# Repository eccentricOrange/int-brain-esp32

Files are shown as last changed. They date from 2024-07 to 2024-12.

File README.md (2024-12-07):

# Integrated Brain
The Integrated Brain is a custom PCB designed to control, supply power to, and monitor a four-wheeled robot. It's built on a master-slave architecture, with an ESP32 as the slave and an SBC (such as an NVIDIA Jetson or Raspberry Pi) as the master.

## Features
| Feature | Description | Specification |
| --- | --- | --- |
| ESP32 Microcontroller | Header for external ESP32 | **ESP32-WROOM-32** 38-pin dev board |
| Motor Drivers | Built on to the PCB | 4x **DRV8251A**. While the 8251A can provide up to **4.1 A**, the PCB design is compatible with other DRV series drivers too. |
| Motor Indicator LEDs | Built on to the PCB | 4x, user-controllable through the PWM demux. |
| Motor Encoder | Support for external quadrature encoders | Connect through JST-4 connectors, directly to ESP32 GPIO. |
| Motor Current Sense | Built on to the PCB | Using the 8251A's feature, connected to the ESP32 ADCs. Additional support for shunt resistor and current-sense amplifier in case of different motor driver IC. |
| IMU | Headers for external IMU | **MPU9250** connected over I2C0 to the ESP32 |
| Internal power supply | Built on to the PCB | **5V (5A)** (TPS5450 buck) and **3.3V** (AMS1117) power supplies for the ESP32 and other peripherals. |
| SBC Power supply | Built on to the PCB | **5V (5A)** (TPS5450 buck) power supply for the SBC., via USB-A. |
| PWM Demux | Built on to the PCB | **PCA9635** connected over I2C0 to the ESP32. Spare PWM channels are *not* exposed. |

## Overall system architecture
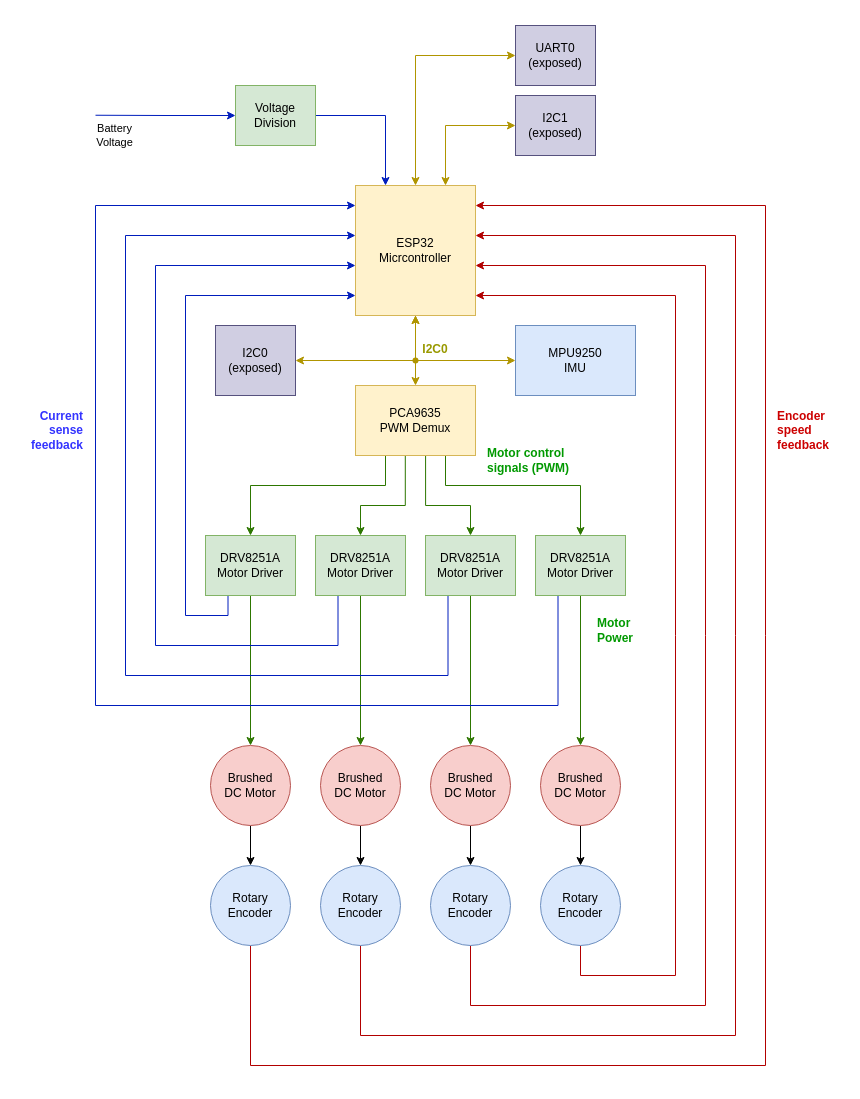
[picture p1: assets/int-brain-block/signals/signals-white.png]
block


The ESP32 microcontroller handles the interaction between all the different peripherals, along with low-level control loops and signal processing. Telemetry and IMU data is fed directly to this ESP32.

Motors are driven using full H-bridge drivers, with built-in braking and current-sense capabilities. These motor drivers are controlled through a PWM demux, owing to the requirement for a large number of PWM pins.

Signals on-board are handled over I2C0, where the ESP32 acts as the master. It is configured as a slave on the I2C1 bus, which is used to communicate with an SBC. I2C0, I2C1, as well as an additional UART port are all exposed with JST connectors.

## Responsibilities of the ESP32 microcontroller
*   Receive commands from the SBC over I2C1
*   Control the motor drivers and the motor indicator LEDs, using the PCA9635 PWM mux over I2C0
*   Read the motor encoders and the motor current sense
*   Read the IMU data, over I2C0
*   Read the battery voltage (using a voltage divider)
*   Run the internal PID loop for motor control (RPM using encoder data)
*   Handle motor protection in case of stall (detected by encoder data) or disconnect (detected by current sense)
*   Filter IMU data
*   Send data to the SBC over I2C1 when requested

## Motor driver design
The system is designed to use the Texas Instruments DRV8251A motor driver, which is capable of driving up to 4.1 A.

Provided that DRV8251A (or any other DRV82\*\*A) drivers are used, we can leverage both the current-sense and current-limiting capabilities of the chip. Since the driver handles current attenuation, we may use a low-power high-resistance shunt resistor to generate a voltage drop. Additionally, using this as a voltage divider, we may supply a current limit; beyond this limit, the driver will automatically throttle voltage.

However, if an alternate motor driver is used (such as DRV8251), the system is designed to support a high-power low-resistance shunt resistor and a current-sense amplifier. The current-limiting feature of the driver will not be used in this case.

The equations to calculate these resistances were derived from the DRV8251A data sheet, and are provided in the schematics.

## Power supply design
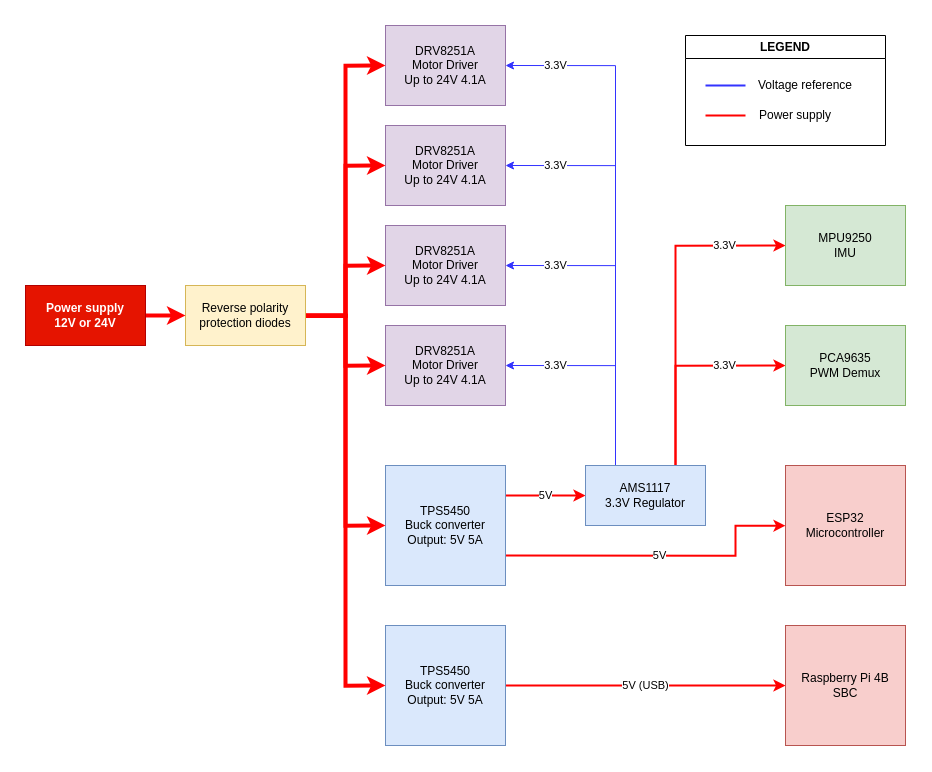
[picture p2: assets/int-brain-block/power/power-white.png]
power


The system is designed to take either 12 V or 24 V DC power. This can be given by either a DC barrel jack or an XT60 connector, designed with the intention of using a LiPo battery. This power must go through two diodes (hooked up in parallel) before being used for any purpose.

Conversion to 5 V and 3.3 V is handled on-board. The buck converter responsible for supplying power to the SBC is isolated from the rest of the system for increased stability.

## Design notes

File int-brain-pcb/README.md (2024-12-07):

# Pin-outs

## IMU MPU9250
| MPU9250 | ESP32 GPIO |
| --- | --- |
| INT | 33 |
| FSYNC | 32 |

Use I2C0 for communication with the IMU.

## Motor Drivers
| Motor | DRV8251A | PCA9685 |
| --- | --- | --- |
| 1A | IN 1 | 12 |
| 1A | IN 2 | 13 |
| 1B | IN 1 | 8 |
| 1B | IN 2 | 9 |
| 2A | IN 1 | 3 |
| 2A | IN 2 | 4 |
| 2B | IN 1 | 5 |
| 2B | IN 2 | 6 |

Use I2C0 for communication with the PCA9685.

## Motor indicator LEDs
| Motor | PCA9685 |
| --- | --- |
| 1A | 11 |
| 1B | 10 |
| 2A | 2 |
| 2B | 7 |

Use I2C0 for communication with the PCA9685.

## Encoders
| Encoder | Pin | ESP32 GPIO |
| --- | --- | --- |
| 1A | 1 | 18 |
| 1A | 2 | 19 |
| 1B | 1 | 23 |
| 1B | 2 | 25 |
| 2A | 1 | 5 |
| 2A | 2 | 17 |
| 2B | 1 | 14 |
| 2B | 2 | 12 |

## Motor current sense
| Motor | ESP32 GPIO |
| --- | --- |
| 1A | 35 |
| 1B | 34 |
| 2A | 39 |
| 2B | 36 |

## Protocols
| Protocol | Pin | ESP32 GPIO | Built-in Pull-up |
| --- | --- | --- | --- |
| I2C0 | SDA | 21 | Yes, 4.7k to 3.3V |
| I2C0 | SCL | 22 | Yes, 4.7k to 3.3V |
| I2C1 | SDA | 13 | Yes, 4.7k to 3.3V |
| I2C1 | SCL | 15 | Yes, 4.7k to 3.3V |
| UART0 | TX | 1 | No |
| UART0 | RX | 3 | No |

Use I2C0 (as master) for communication with the IMU and PCA9685. Use I2C1 (as slave) for communication with an SBC such as a Raspberry Pi or NVIDIA Jetson.

## Miscellaneous
| Function | ESP32 GPIO |
| --- | --- |
| Battery Voltage | 25 |
| Motor PCA Enable | 4 |

# Screenshots

PCB Front
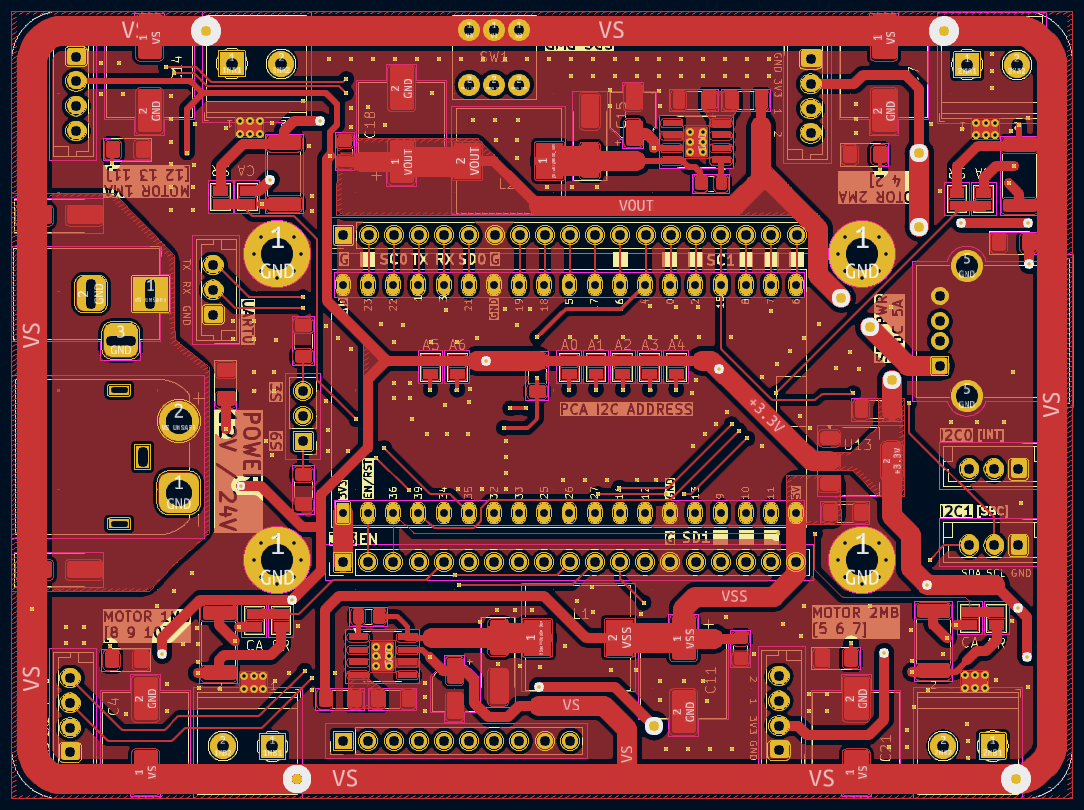
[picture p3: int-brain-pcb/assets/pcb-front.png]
pcb-front


PCB Back
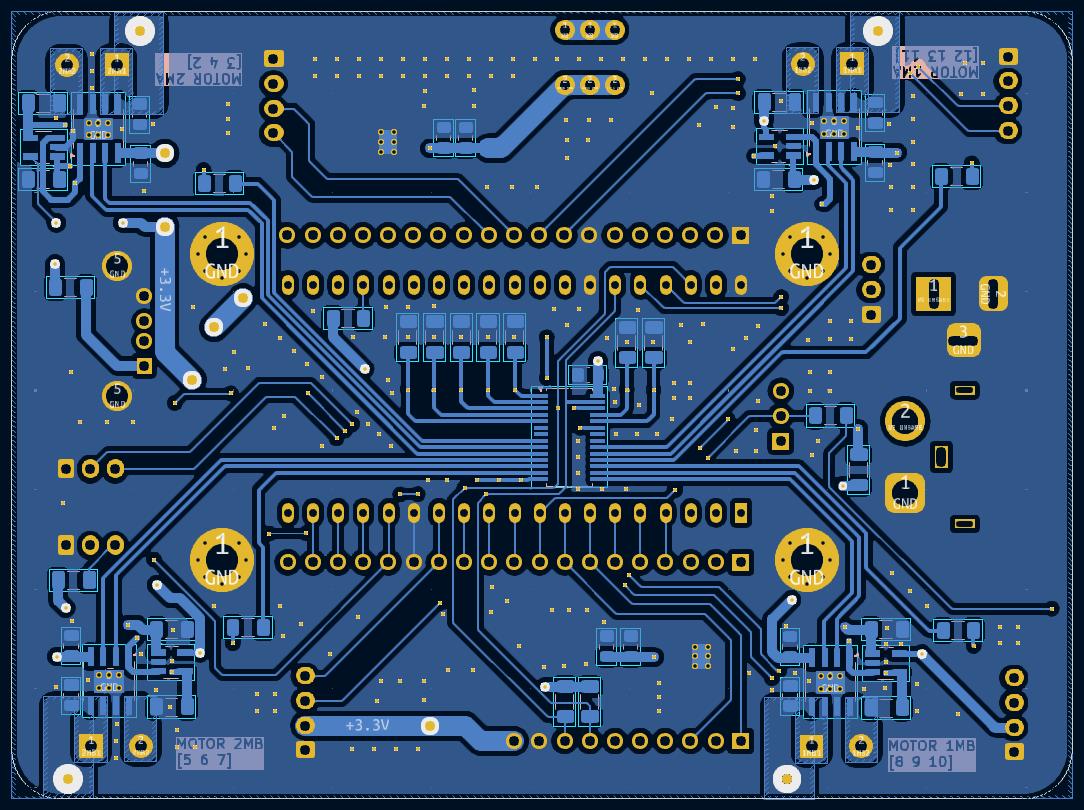
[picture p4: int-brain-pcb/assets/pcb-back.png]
pcb-back


3D Front
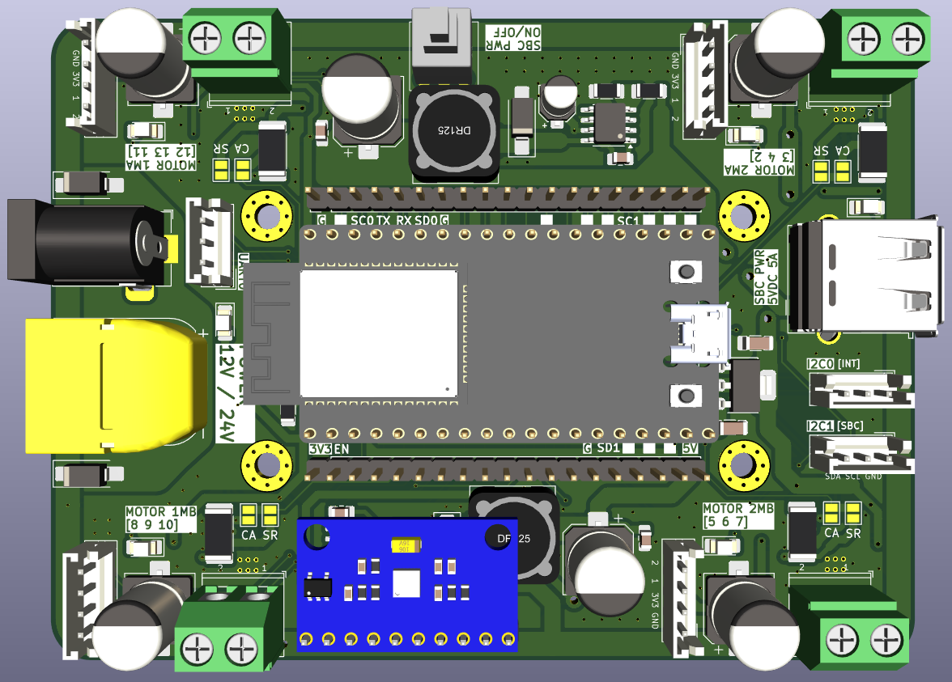
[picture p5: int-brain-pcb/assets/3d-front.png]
3d-front


3D Back
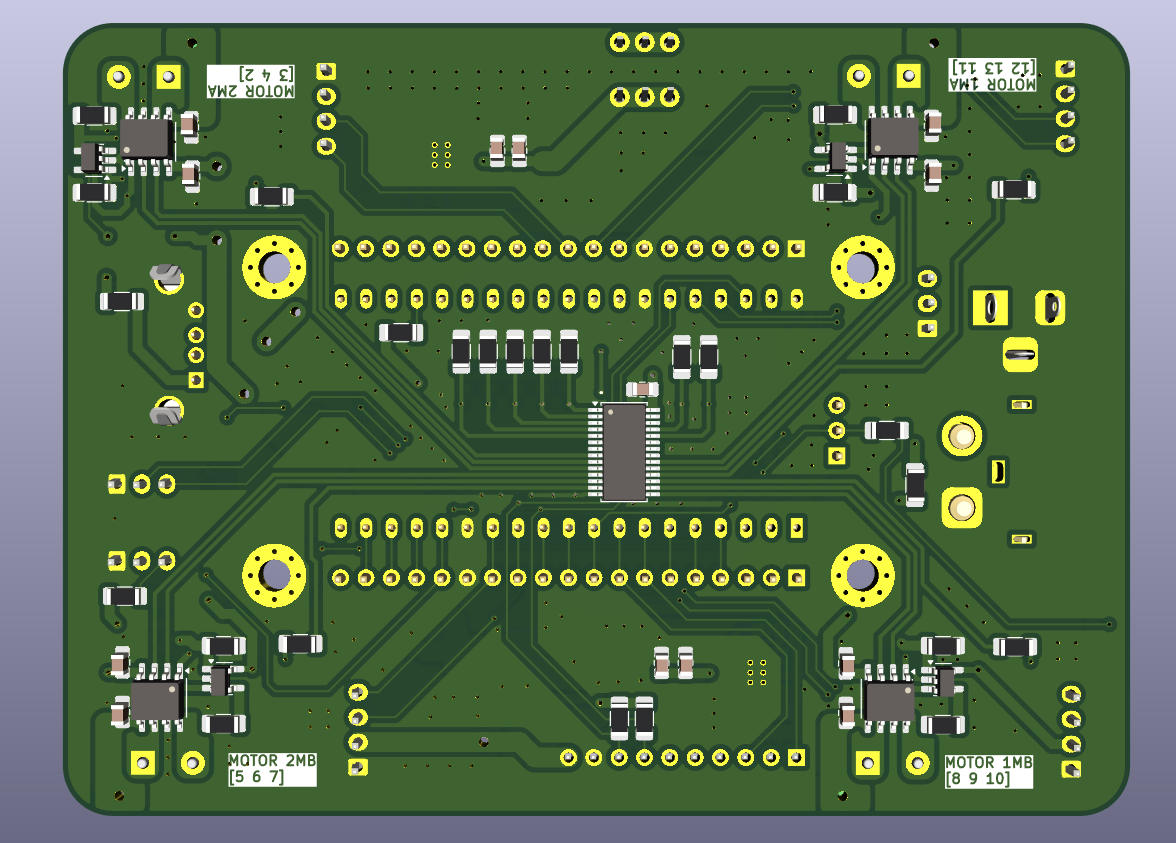
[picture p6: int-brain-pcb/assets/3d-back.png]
3d-back


3D Angled
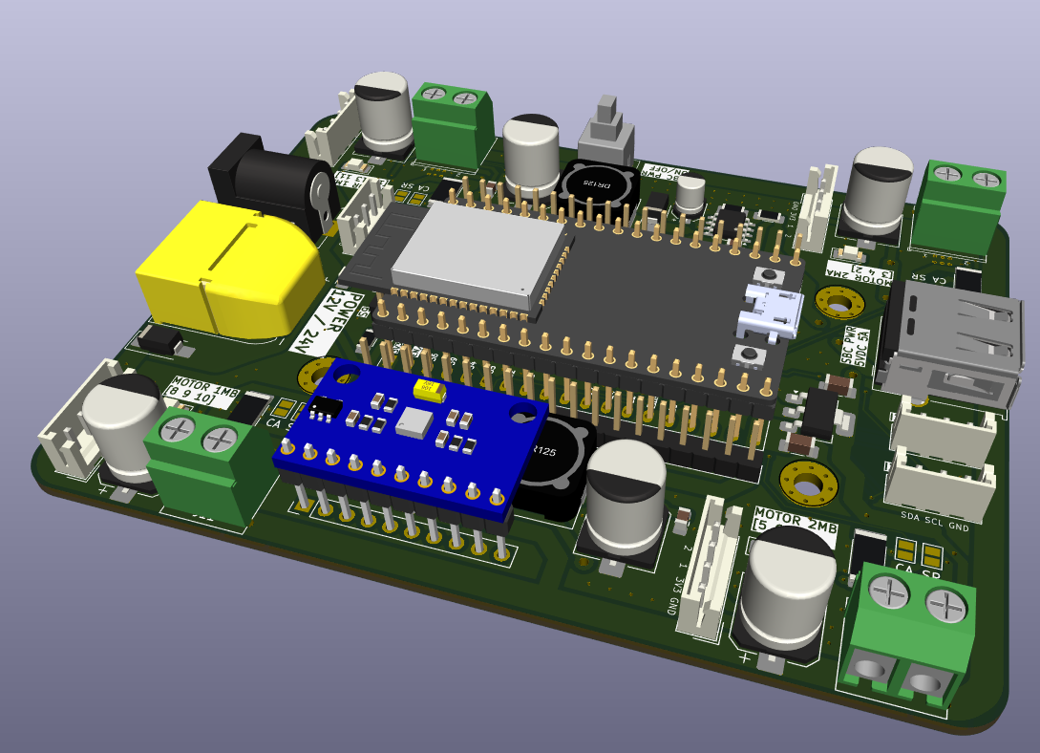
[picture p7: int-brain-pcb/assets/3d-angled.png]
3d-angled


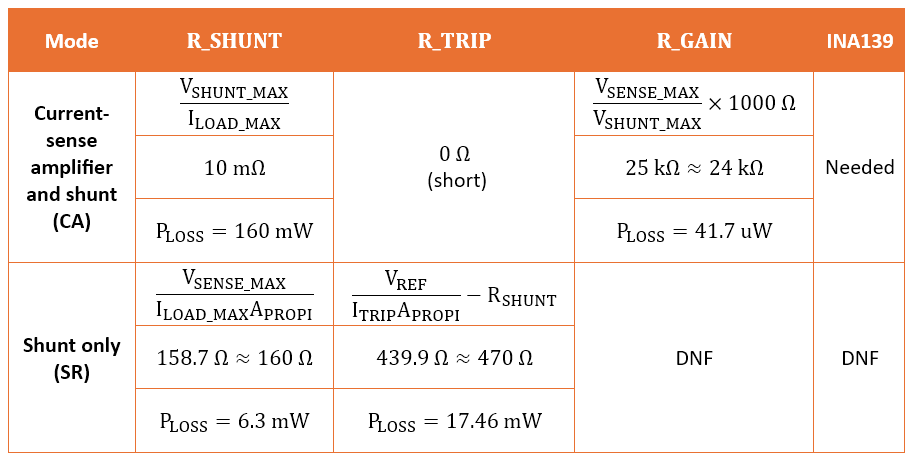
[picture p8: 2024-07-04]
int-brain-pcb/assets/calculated-values.png

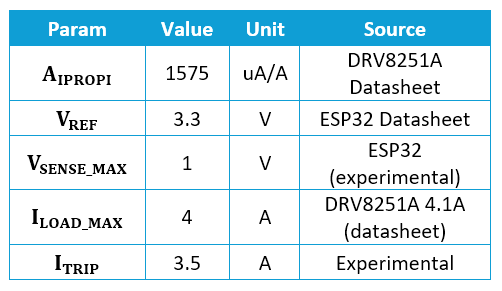
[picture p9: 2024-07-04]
int-brain-pcb/assets/assumed-values.png

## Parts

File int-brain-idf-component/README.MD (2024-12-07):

# Integrated Brain ESP-IDF Component
This is the MCU firmware for a custom PCB designed to control, supply power to, and monitor a four-wheeled robot. It's built on a master-slave architecture, with an ESP32 as the slave and an SBC (such as an NVIDIA Jetson or Raspberry Pi) as the master.

Note that this project has a lot of different registers, addresses, and buffers. These are referenced several times throughout the documentation, but in the interest of comprehensibility, they are all listed towards the end of the documentation only.

# Overall design
Let's get an overview of the different concepts and categories of stuff (such as functions) involved in this component.

## Direct and register-based tasks
In general, there are two types of functions in the component:

-   **Direct task**

    These functions are typical functions. You call them (and pass in arguments if relevant) and the function will try to do whatever you told it to. Exactly how it behaves is completely transparent in this scenario: for example, if you told motor 3 to move forward with a PWM of 127, that's exactly what the system will attempt to do, and nothing else.

-   **Register-based task**

    In the interest of having a flexible system that can establish duplex (two-way) communication with an SBC, there is an extensive system of registers and state variables. Many functions write to these, and many others read from them to decide what actions to perform. You (the programmer) doesn't have the luxury of specifying the 127 (PWM) or forward (direction) as literal values in this situation.

The Doxygen documentation for each function states its type, so you can easily tell which is which.

## Topics/themes

*   **PCA9635 PWM Demux**

    To overcome the low number of GPIOs in the ESP32, this project uses the PCA driver to give PWM signals to the motor drivers and their corresponding LEDs. There are methods around initializing the driver, setting it's mode, setting specific PWM values etc. These are all under `pca_driver.h`.

*   **Current sense**

    The motor drivers have a current sense output that can be read by the ESP32 (with the use of a shunt resistor). The current sense is read by the ADC and converted to a digital value. The initialization, calibration, and reading of the current sense are all under `current_sense.h`.

*   **Encoder**
    
    The motors have encoders that can be read by the ESP32 to provide their angular velocity. The initialization, reading, and resetting of the encoders are all under `encoder.h`.

*   **Control of the robot and that of the motors is separate**

    The PCA drivers file `pca_driver.h` is responsible for controlling the motors and LEDs, and tends to deal with the lower-level functions of one motor at a time. The `four-wheel-robot.h` file is responsible for controlling four motors at a time, and includes some functions to instead treat the system as a cohesive robot. Functions in `four-wheel-robot.h` use functions from `pca_driver.h` quite heavily.

*   **Structure**

    In general, "direct" functions are used to handle things like initialization and register-based functions are used to handle the actual tasks. Either these functions directly, or your custom functions, are expected to be registered as RTOS tasks using `xTaskCreate()` (built-in to FreeRTOS and ESP-IDF) since they will run perpetually.

# I2C Communication with the SBC
This is one of the relatively elaborate parts of the firmware, so it deserves some more attention. In general, the ESP32 acts as a slave to the SBC. The SBC can both issue commands to the ESP32, and request data such as sensor readings and motor status.

It is important you understand how this works, so we'll go over it in detail.

*   **The concept of a pseudo register**

    In the world of I2C-based devices, it is common for the slave to have a register. Each register then has a defined memory location (an address) and a clear purpose. For example, setting the value of the register at `0x00` sets the PCA driver mode, telling it what to do with further commands from the master.

    Since there is a wide variety of data we wish to transfer between the ESP32 and the SBC, this project adopts a similar system. Instead of dealing with actual memory addresses in the ESP32, we use a "pseudo register" system. To the SBC, this seems as though the ESP32 has registers like any ol' I2C device. However, in reality, it just places the byte that's supposed to the register address into a `switch() case` structure.

    Many other functions in the firmware behave in that way, so it's important to recognize what the term "register" refers to in this system. Unfortunately, devices like the PCA driver and the IMU do have true registers, so I'll provide a list of all pseudo later in this documentation.

    `int-brain-sbc-registers.h` gives the addresses of most of these pseudo registers that the SBC has to deal with. Additionally, addresses are split into sending and receiving addresses, to make it easier to determine what the I2C bus is doing at any given time.

*   **I2C buffers**

    Additionally, whenever the master (SBC) initiates a communication, it is expected that the first byte is the pseudo register address. The ESP32 will then read this byte and decide what to do based on it. While parsing, this byte is stored in `_sbc_i2c1_register`.

    Keeping in mind the interrupt-based nature of I2C communication in the ESP32 system \[[source](https://docs.espressif.com/projects/esp-idf/en/v5.3/esp32/api-reference/peripherals/i2c.html)\], two I2C buffers are defined in this system.

    *   One of them `_sbc_i2c1_receive_buffer` is the data (such as motor speeds) that should go from the SBC to the ESP32. When the ESP32 has finished reading the data, it is available in this buffer.
    *   The other `_sbc_i2c1_send_buffer` is the data (such as encoder positions) that should go from the ESP32 to the SBC. While parsing the pseudo register `_sbc_i2c1_register`, the ESP32 will fill this buffer with the relevant data, and the master can read it whenever it wants. Note that this is a FIFO buffer, so care should be taken that whatever data is written to it is read by the master (and not left to clog up the buffer).

# Motor command systems
Controlling a motor has two basic aspects: the direction and the speed, given as forward/backward/stop and a PWM value respectively.

Motor modes allow us to incorporate more functionality that can help in development of more safety features, make it easier to take emergency action, and issue the same speed to all motors at once.

These modes are controlled by a pseudo register, and pairs of bits define each mode.

## Safety modes
*   **Unsafe mode**

    The motor obeys your commands directly, without any modifications from the firmware. This is the default mode.

*   **Protect stall mode**
    
    A stall is defined either when the motor exceeds a certain current threshold or when the encoder position is not changing, given a PWM value. To protect the motor, it will be stopped if a stall is detected.

*   **Protect disconnect mode**
    
    If the motor is disconnected, the current sense will read zero, given a minimum PWM value. If this is detected, the motor will be stopped. Optionally, that specific motor's LED will blink to let you debug easily.

*   **Protect stall and disconnect mode**
        
    This is a combination of the two modes above. If either a stall or a disconnect is detected, the motor will be stopped.

## Speed modes
*   **Stop mode:** The motor will stop, regardless of the PWM value (PWM = 0).
*   **Max mode:** The motor will run at full speed, regardless of the PWM value (PWM = 255).
*   **Command speed mode:** The motor will run at the PWM value you specify for that particular motor.
*   **Speed register mode:** All motors will run at the same speed, given by the value in the speed register.

## Enable modes
This leverages the OUTPUT ENABLED pin of the PCA driver. If the driver is disabled, all PWM values will be 0, and all motors will stop.

This value for this mode may simply be enabled or disabled.

## Motor direction
The DRV8251A driver has the ability to actively brake the motor instead of letting it coast to a stop. This is done by setting the direction to brake. This gives us a total of four possible directions for each motor: idle, forward, backward, and brake.

## Motor command functions

| Function name | Speed control type | Direction control type | Safety mode | Speed mode | Enable mode |
| --- | --- | --- | --- | --- | --- |
| `set_motor_speeds()` | Array for individual speeds | [unused] | Not set-able | Not set-able | Not set-able |
| `set_common_motor_speed()` | Single speed for all motors | [unused] | Not set-able | Not set-able | Not set-able |
| `set_motor_directions()` | [unused] | Array for individual directions | Not set-able | Not set-able | Not set-able |
| `set_bot_direction()` | [unused] | Variable for unified robot direction | Not set-able | Not set-able | Not set-able |
| `set_motor_mode_register()` | [unused] | [unused] | Set-able by variable | Set-able by variable | Set-able by variable |
| `set_motor_safety_mode()` | [unused] | [unused] | Set-able by variable | [unused] | [unused] |
| `set_motor_speed_mode()` | [unused] | [unused] | [unused] | Set-able by variable | [unused] |
| `enable_motor_output()` | [unused] | [unused] | [unused] | [unused] | Forced to `ENABLED` |
| `disable_motor_output()` | [unused] | [unused] | [unused] | [unused] | Forced to `DISABLED` |

After calling any of these, you must also call `publish_motor_command()` to actually send the commands to the motors through the PCA driver.

# I2C Scheme

## Addresses

| Host | Slave | Address |
| --- | --- | --- |
| ESP32 | MPU9250 | 0x68 or 0x69 |
| ESP32 | PCA9635 | 0x40 |
| Raspberry Pi | ESP32 | 0x30 |

Note that in many of the registers below, the address is given as a range. In such cases, each address in range corresponds to a particular motor. This feature allows you to use a shorter I2C transmission if you do not want to address all motors at once.

## Raspberry Pi request from ESP32 (send) registers
*   `FIRST_SLAVE_REQUEST_ADDRESS = 0x20`
*   `LAST_SLAVE_REQUEST_ADDRESS = 0x9F`

| Description | "Register" | Data type | Length |
| --- | --- | --- | --- |
| Encoder positions | 0x20 | 4 bytes per motor (int) | 16 bytes |
| Encoder position per motor | 0x21 - 0x24 | 4 bytes (int) | 4 bytes |
| Motor speeds | 0x25 | 4 bytes per motor (int) | 16 bytes |
| Motor speed per motor | 0x26 - 0x29 | 4 bytes (int) | 4 bytes |
| Motor current | 0x30 | 4 bytes per motor (int) | 16 bytes |
| Motor current per motor | 0x31 - 0x34 | 4 bytes (int) | 16 bytes |
| Motor stall status | 0x40 | 1 byte total (bool) | 1 byte |
| Motor disconnect status | 0x41 | 1 byte total (bool) | 1 byte |
| IMU data (acceleration) | 0x50 | 4 bytes per axis (int) | 12 bytes |
| IMU data (gyroscope) | 0x51 | 4 bytes per axis (int) | 12 bytes |
| IMU data (magnetometer) | 0x52 | 4 bytes per axis (int) | 12 bytes |
| IMU data (quaternion) | 0x53 | 4 bytes per axis (int) | 16 bytes |
| Battery voltage | 0x60 | 4 bytes (int) | 4 bytes |

## Raspberry Pi command to ESP32 (receive) registers
*   `FIRST_SLAVE_COMMAND_ADDRESS = 0xA0`
*   `LAST_SLAVE_COMMAND_ADDRESS = 0xFF`

| Description | "Register" | Data type | Length |
| --- | --- | --- | --- |
| Motor operation mode | 0xA0 | 1 byte total (int) | 1 byte |
| Standard motor data | 0xA1 | 1 byte per motor + 1 byte (int + int) | 5 bytes |
| Standard motor data per motor | 0xA2 - 0xA5 | 2 bytes (int + int) | 2 bytes |
| Motor directions | 0xA6 | 1 byte total (int) | 1 byte |
| Motor direction per motor | 0xA7 - 0xAA | 1 byte (int) | 1 byte |
| Motor speeds | 0xAB | 1 byte per motor (int) | 4 bytes |
| Motor speed per motor | 0xAC - 0xAF | 1 byte (int) | 1 byte |
| Robot direction | 0xB0 | 1 byte total (int) | 1 byte |
| Common speed | 0xB1 | 2 bytes (int) | 2 bytes |

The "standard motor data" is simply means that the first byte specifies motor direction and next byte(s) specify the motor speed(s). This functionality is made available since it's common to send both these parameters together in practical robots.

## Bit breakdowns

### [0xB0] Robot direction
| Value | Description |
| --- | --- |
| 0 | Front |
| 1 | Back |
| 2 | Rotate clockwise |
| 3 | Rotate counterclockwise |
| 4 | Front left |
| 5 | Front right |
| 6 | Back left |
| 7 | Back right |

### [Common motor breakdown]
The motor stall status, disconnect status, and direction registers all obey this scheme. Two bits are used to specify the value for any one motor, so a single byte is sufficient for all four motors.

| Bit | Motor |
| --- | --- |
| 0, 1 | 0 |
| 2, 3 | 1 |
| 4, 5 | 2 |
| 6, 7 | 3 |

### [0x30] Motor stall status
| Value | Description |
| --- | --- |
| 00 | Not stalled |
| 01 | Stalled |
| 10 | [UNUSED] |
| 11 | [UNUSED] |

### [0x31] Motor disconnect status
| Value | Description |
| --- | --- |
| 00 | Connected |
| 01 | Disconnected |
| 10 | [UNUSED] |
| 11 | [UNUSED] |

### [0xA6] Motor directions
| Value | Description |
| --- | --- |
| 00 | Idle |
| 01 | Forward |
| 10 | Backward |
| 11 | Brake |

### [0xA0] Motor operation mode
This register does not follow the common motor breakdown scheme. Instead, each pair of bits controls a different aspect of the motor operation mode. The modes set here apply to all motors.

#### Bits 1, 0: Safety
| Value | Description |
| --- | --- |
| 00 | Unsafe |
| 01 | Protect stall |
| 10 | Protect disconnect |
| 11 | Protect stall and disconnect |

#### Bits 3, 2: Speed
| Value | Description |
| --- | --- |
| 00 | 0 (stop) |
| 01 | 255 (max) |
| 10 | command speed |
| 11 | speed register (0xB1) |

#### Bit 5, 4: Enable
| Value | Description |
| --- | --- |
| 00 | Disable |
| 01 | Enable |
| 10 | [UNUSED] |
| 11 | [UNUSED] |

#### Bits 6 - 7: Unused

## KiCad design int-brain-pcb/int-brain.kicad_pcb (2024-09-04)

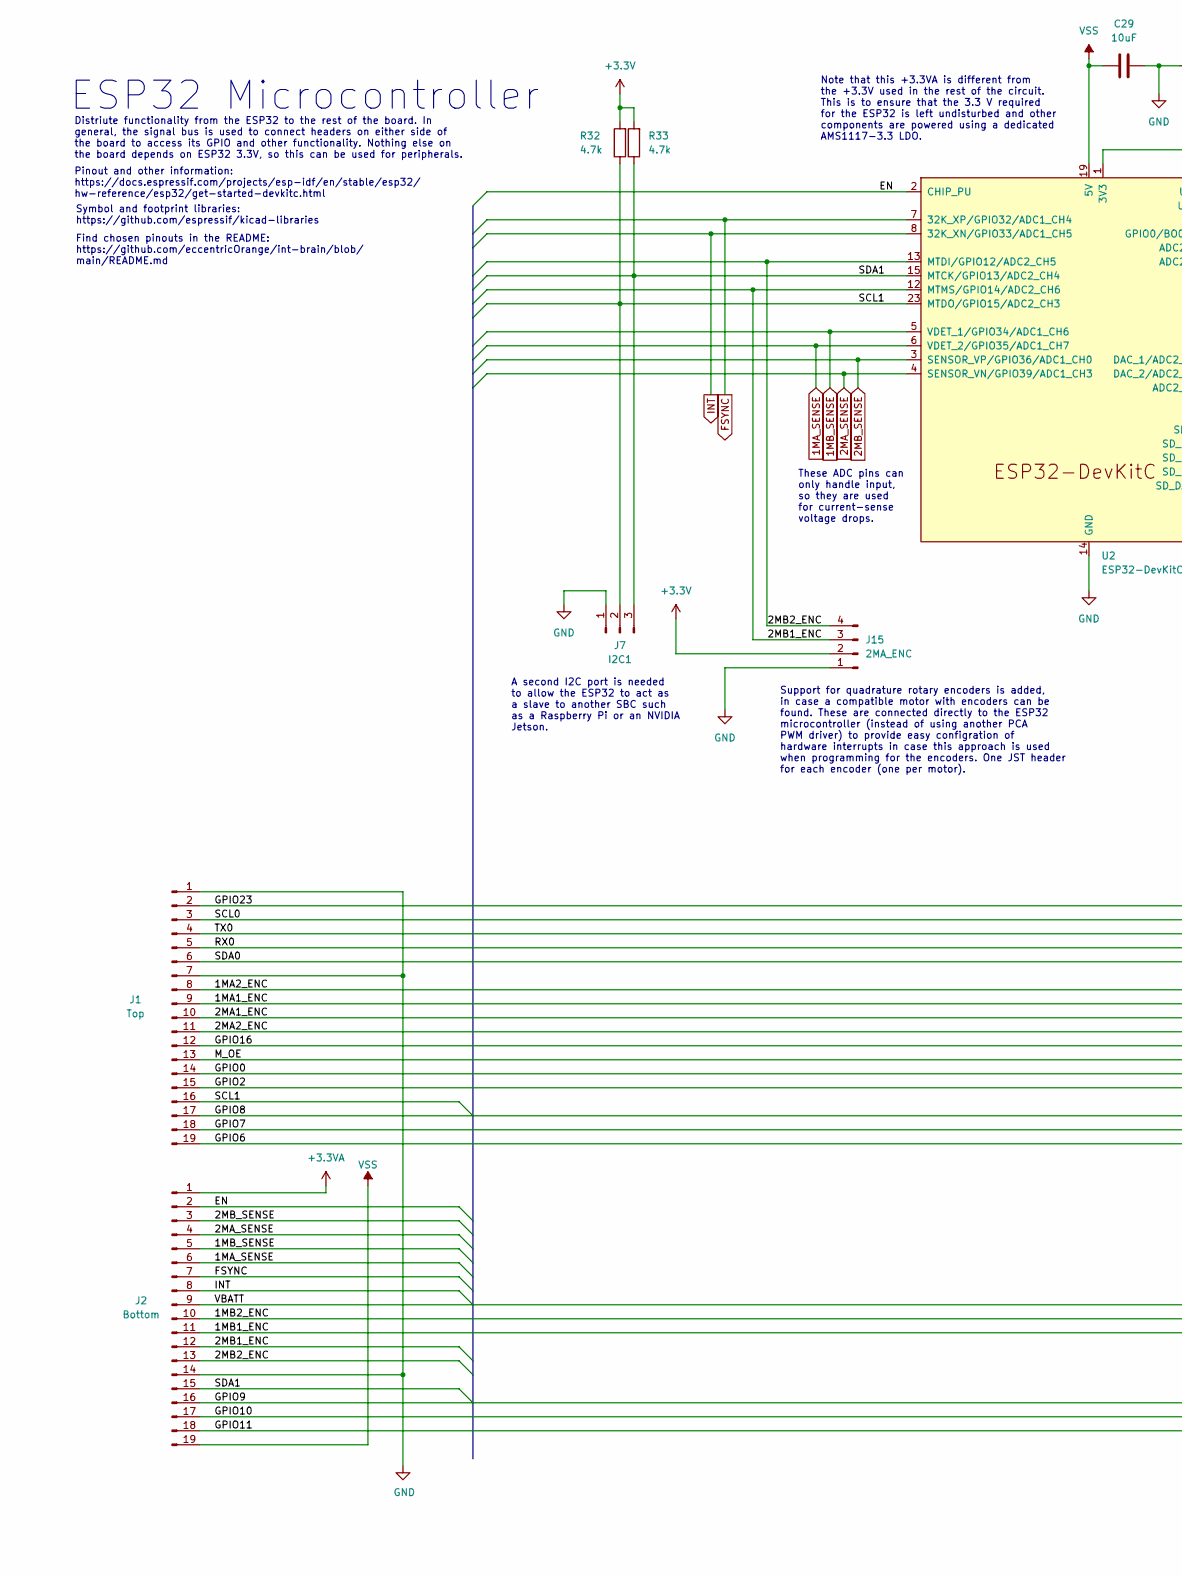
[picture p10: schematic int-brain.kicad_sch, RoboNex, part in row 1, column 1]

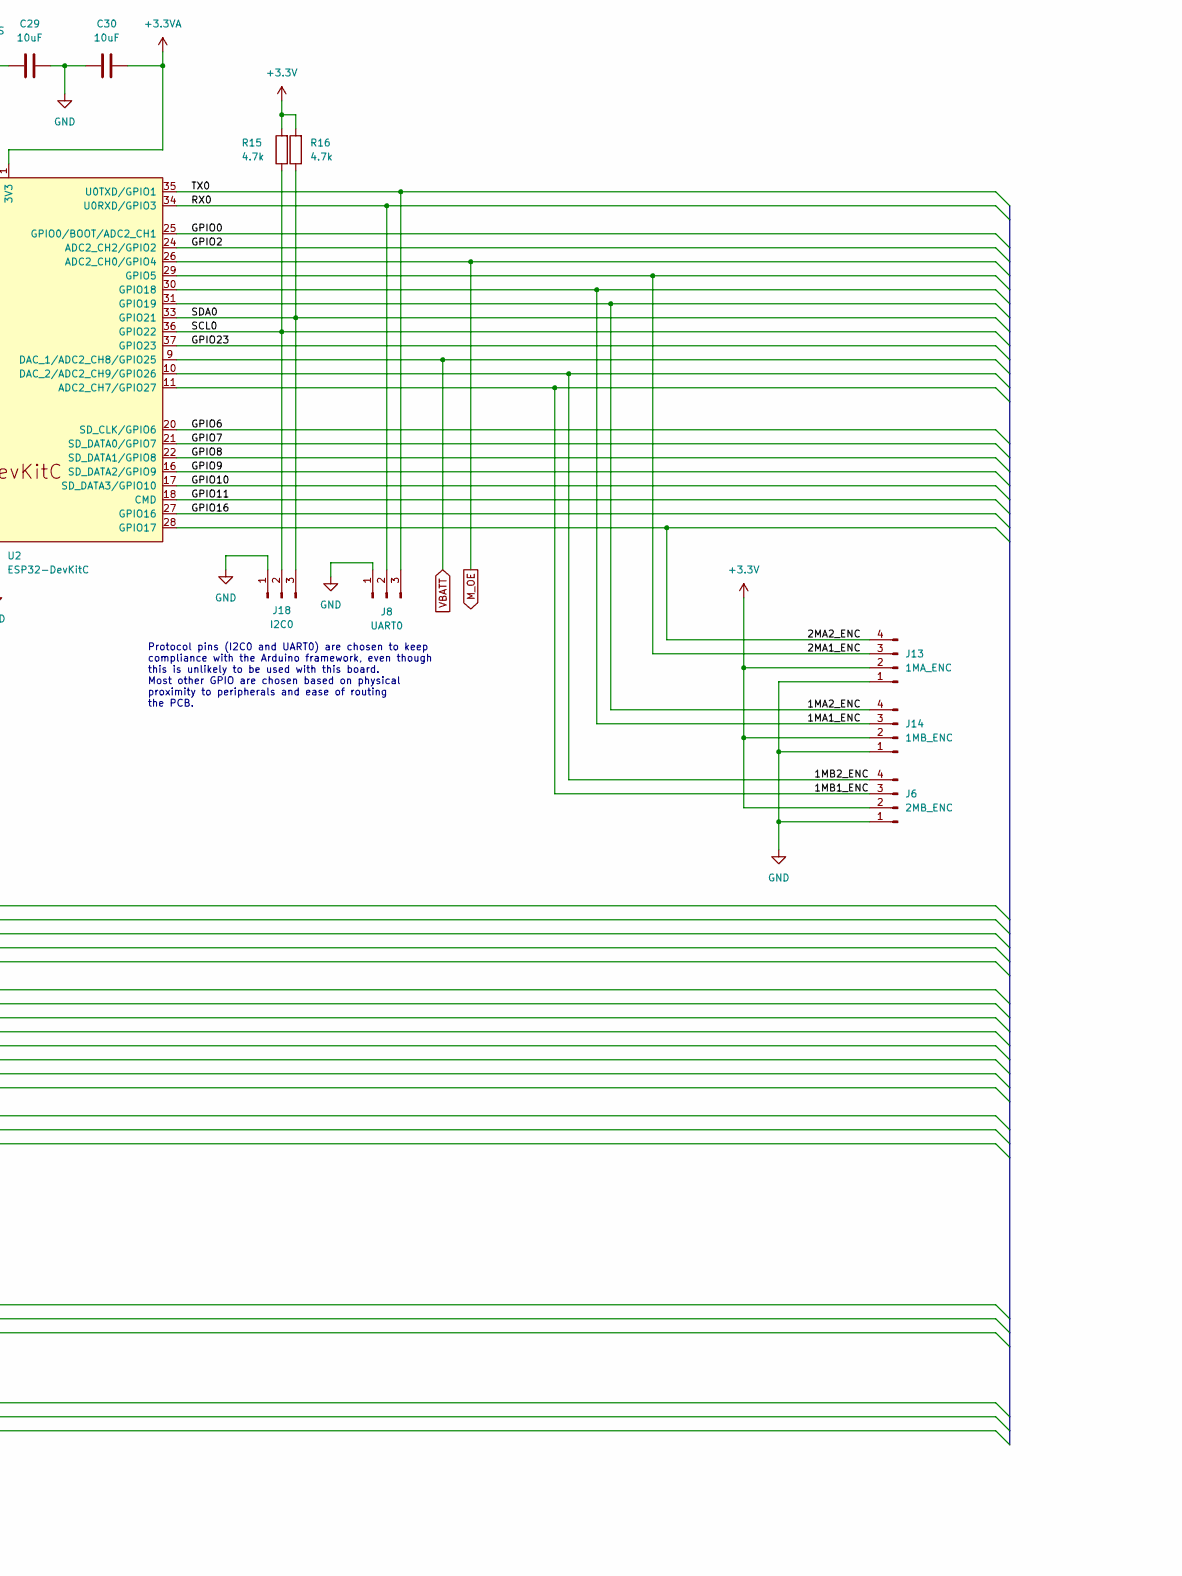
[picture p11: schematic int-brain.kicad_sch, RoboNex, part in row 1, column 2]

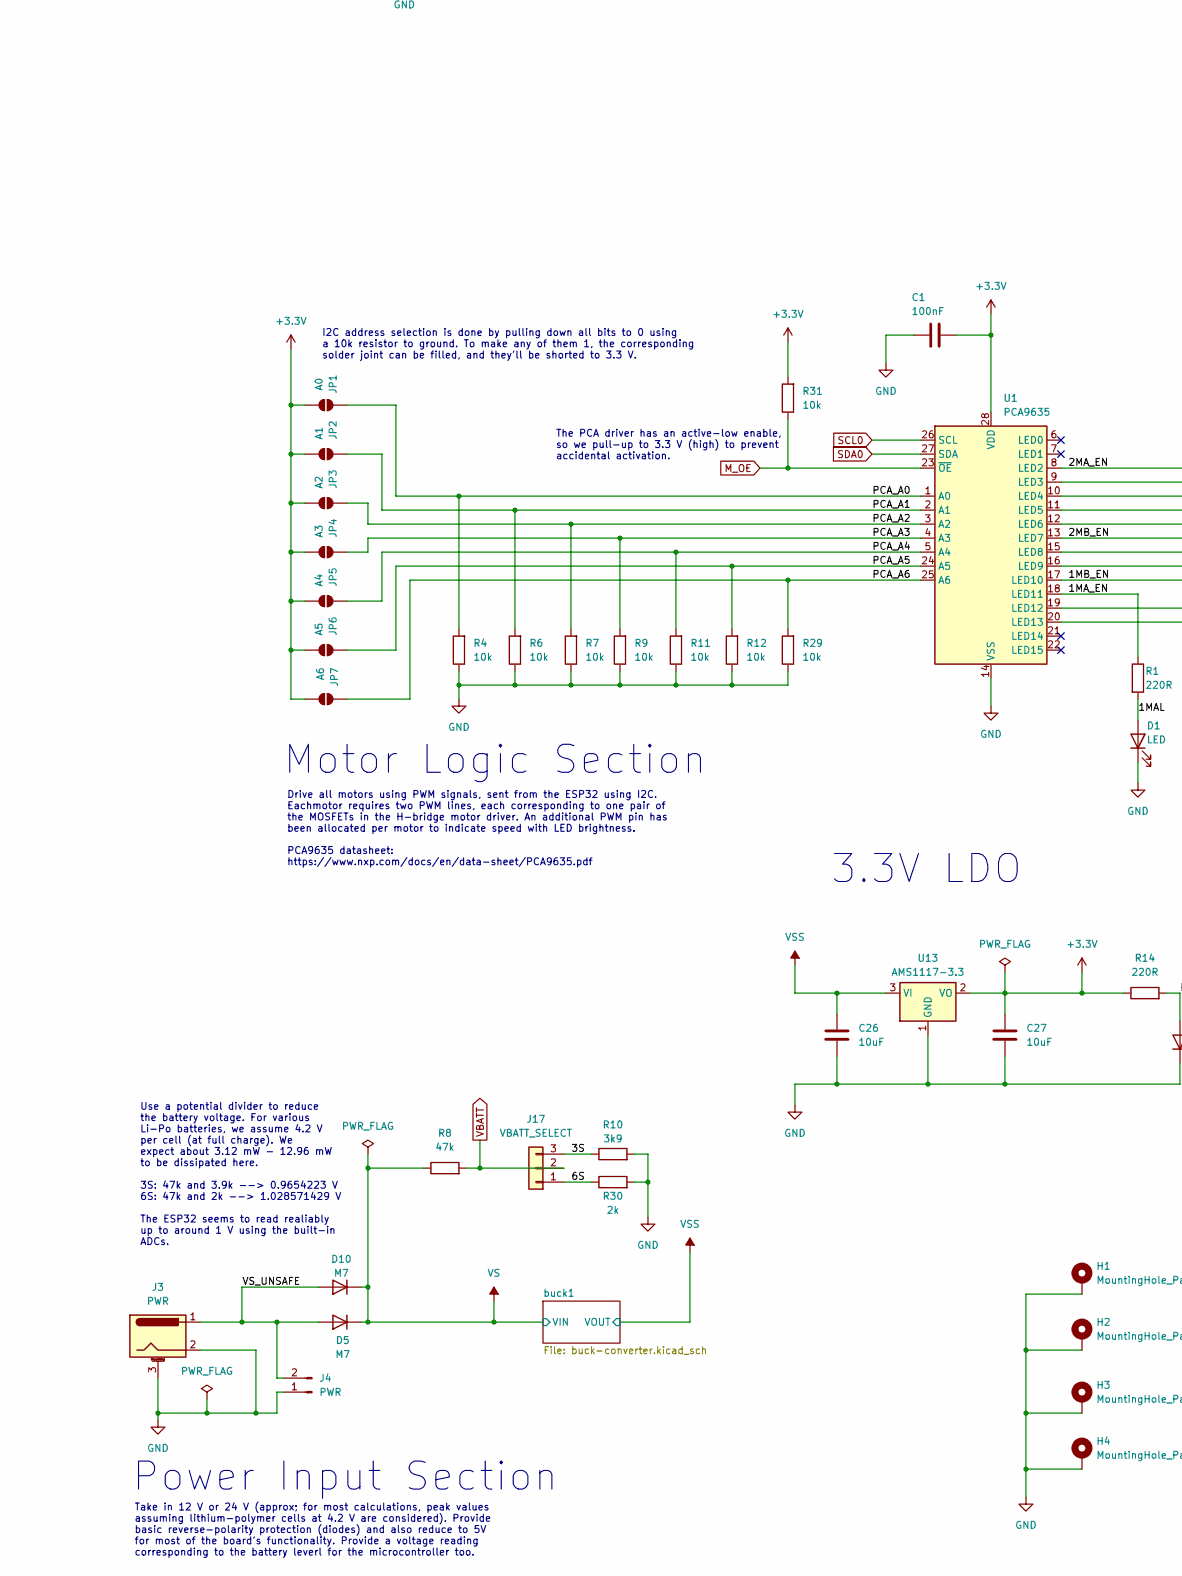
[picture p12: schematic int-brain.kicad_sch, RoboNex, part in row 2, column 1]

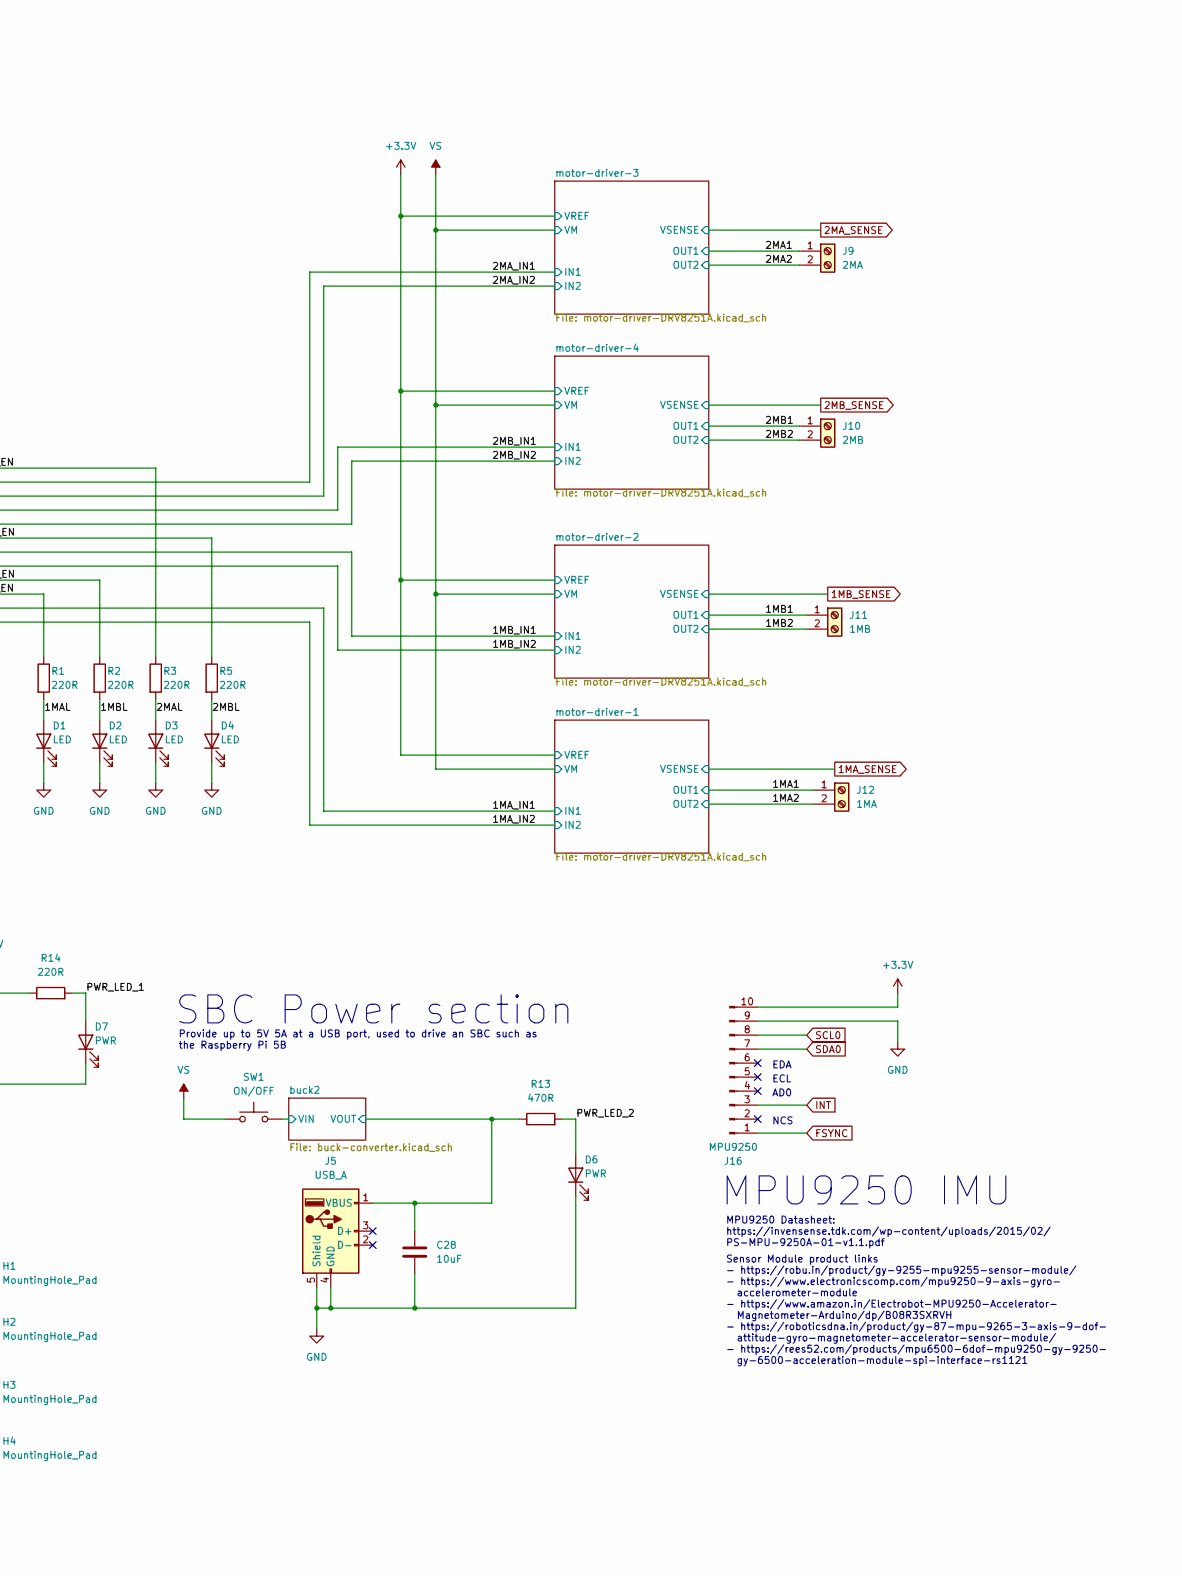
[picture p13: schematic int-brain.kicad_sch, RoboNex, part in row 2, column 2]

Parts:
C1: 100nF; C_0805_2012Metric_Pad1.18x1.45mm_HandSolder
C26, C27, C28, C29, C30: 10uF; C_1206_3216Metric_Pad1.33x1.80mm_HandSolder
D1, D2, D3, D4: LED; LED_1206_3216Metric_Pad1.42x1.75mm_HandSolder
D5, D10: M7; D_SMA_Handsoldering
D6, D7: PWR; LED_1206_3216Metric_Pad1.42x1.75mm_HandSolder
H1, H2, H3, H4: MountingHole_Pad; MountingHole_3.2mm_M3_Pad_Via
J1: Top; PinHeader_1x19_P2.54mm_Vertical
J2: Bottom; PinHeader_1x19_P2.54mm_Vertical
J3: PWR; BarrelJack_Horizontal
J4: PWR; AMASS_XT60IPW-M_1x03_P7.20mm_Horizontal
J5: USB_A; USB_A_Molex_67643_Horizontal
J6: 2MB_ENC; JST_EH_B4B-EH-A_1x04_P2.50mm_Vertical
J7: I2C1; JST_EH_B3B-EH-A_1x03_P2.50mm_Vertical
J8: UART0; JST_EH_B3B-EH-A_1x03_P2.50mm_Vertical
J9: 2MA; TerminalBlock_Philmore_TB132_1x02_P5.00mm_Horizontal
J10: 2MB; TerminalBlock_Philmore_TB132_1x02_P5.00mm_Horizontal
J11: 1MB; TerminalBlock_Philmore_TB132_1x02_P5.00mm_Horizontal
J12: 1MA; TerminalBlock_Philmore_TB132_1x02_P5.00mm_Horizontal
J13: 1MA_ENC; JST_EH_B4B-EH-A_1x04_P2.50mm_Vertical
J14: 1MB_ENC; JST_EH_B4B-EH-A_1x04_P2.50mm_Vertical
J15: 2MA_ENC; JST_EH_B4B-EH-A_1x04_P2.50mm_Vertical
J16: MPU9250; PinHeader_1x10_P2.54mm_Vertical
J17: VBATT_SELECT; PinHeader_1x03_P2.54mm_Vertical
J18: I2C0; JST_EH_B3B-EH-A_1x03_P2.50mm_Vertical
JP1: A0; SolderJumper-2_P1.3mm_Open_Pad1.0x1.5mm
JP2: A1; SolderJumper-2_P1.3mm_Open_Pad1.0x1.5mm
JP3: A2; SolderJumper-2_P1.3mm_Open_Pad1.0x1.5mm
JP4: A3; SolderJumper-2_P1.3mm_Open_Pad1.0x1.5mm
JP5: A4; SolderJumper-2_P1.3mm_Open_Pad1.0x1.5mm
JP6: A5; SolderJumper-2_P1.3mm_Open_Pad1.0x1.5mm
JP7: A6; SolderJumper-2_P1.3mm_Open_Pad1.0x1.5mm
R1, R2, R3, R5, R14: 220R; R_1206_3216Metric_Pad1.30x1.75mm_HandSolder
R4, R6, R7, R9, R11, R12, R29, R31: 10k; R_1206_3216Metric_Pad1.30x1.75mm_HandSolder
R8: 47k; R_1206_3216Metric_Pad1.30x1.75mm_HandSolder
R10: 3k9; R_1206_3216Metric_Pad1.30x1.75mm_HandSolder
R13: 470R; R_1206_3216Metric_Pad1.30x1.75mm_HandSolder
R15, R16, R32, R33: 4.7k; R_1206_3216Metric_Pad1.30x1.75mm_HandSolder
R30: 2k; R_1206_3216Metric_Pad1.30x1.75mm_HandSolder
SW1: ON/OFF; SW_PUSH_6mm_H5mm
U1: PCA9635; TSSOP-28_4.4x9.7mm_P0.65mm
U2: ESP32-DevKitC; ESP32-DevKitC-slim
U13: AMS1117-3.3; SOT-223-3_TabPin2

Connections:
1MA_SENSE: J2.6, U2.6 (VDET_2/GPIO35/ADC1_CH7); also elsewhere on the board
1MB_SENSE: J2.5, U2.5 (VDET_1/GPIO34/ADC1_CH6); also elsewhere on the board
2MA_SENSE: J2.4, U2.4 (SENSOR_VN/GPIO39/ADC1_CH3); also elsewhere on the board
2MB_SENSE: J2.3, U2.3 (SENSOR_VP/GPIO36/ADC1_CH0); also elsewhere on the board
+3.3V: C1.1, C27.1, J6.2, J13.2, J14.2, J15.2, J16.10, JP1.1 (A), JP2.1 (A), JP3.1 (A), JP4.1 (A), JP5.1 (A), JP6.1 (A), JP7.1 (A), R14.1, R15.2, R16.2, R31.2, R32.2, R33.2, U1.28 (VDD), U13.2 (VO); also elsewhere on the board
+3.3VA: C30.2, J2.1, U2.1 (3V3)
/1MA1: J12.1; also elsewhere on the board
/1MA1_ENC: J1.9, J14.3, U2.30 (GPIO18)
/1MA2: J12.2; also elsewhere on the board
/1MA2_ENC: J1.8, J14.4, U2.31 (GPIO19)
/1MAL: D1.2 (A), R1.2
/1MA_EN: R1.1, U1.18 (LED11)
/1MA_IN1: U1.19 (LED12); also elsewhere on the board
/1MA_IN2: U1.20 (LED13); also elsewhere on the board
/1MB1: J11.1; also elsewhere on the board
/1MB1_ENC: J2.11, J6.3, U2.11 (ADC2_CH7/GPIO27)
/1MB2: J11.2; also elsewhere on the board
/1MB2_ENC: J2.10, J6.4, U2.10 (DAC_2/ADC2_CH9/GPIO26)
/1MBL: D2.2 (A), R2.2
/1MB_EN: R2.1, U1.17 (LED10)
/1MB_IN1: U1.15 (LED8); also elsewhere on the board
/1MB_IN2: U1.16 (LED9); also elsewhere on the board
/2MA1: J9.1; also elsewhere on the board
/2MA1_ENC: J1.10, J13.3, U2.29 (GPIO5)
/2MA2: J9.2; also elsewhere on the board
/2MA2_ENC: J1.11, J13.4, U2.28 (GPIO17)
/2MAL: D3.2 (A), R3.2
/2MA_EN: R3.1, U1.8 (LED2)
/2MA_IN1: U1.9 (LED3); also elsewhere on the board
/2MA_IN2: U1.10 (LED4); also elsewhere on the board
/2MB1: J10.1; also elsewhere on the board
/2MB1_ENC: J2.12, J15.3, U2.12 (MTMS/GPIO14/ADC2_CH6)
/2MB2: J10.2; also elsewhere on the board
/2MB2_ENC: J2.13, J15.4, U2.13 (MTDI/GPIO12/ADC2_CH5)
/2MBL: D4.2 (A), R5.2
/2MB_EN: R5.1, U1.13 (LED7)
/2MB_IN1: U1.11 (LED5); also elsewhere on the board
/2MB_IN2: U1.12 (LED6); also elsewhere on the board
/3S: J17.3, R10.1
/6S: J17.1, R30.1
/EN: J2.2, U2.2 (CHIP_PU)
/GPIO0: J1.14, U2.25 (GPIO0/BOOT/ADC2_CH1)
/GPIO2: J1.15, U2.24 (ADC2_CH2/GPIO2)
/GPIO6: J1.19, U2.20 (SD_CLK/GPIO6)
/GPIO7: J1.18, U2.21 (SD_DATA0/GPIO7)
/GPIO8: J1.17, U2.22 (SD_DATA1/GPIO8)
/GPIO9: J2.16, U2.16 (SD_DATA2/GPIO9)
/GPIO10: J2.17, U2.17 (SD_DATA3/GPIO10)
/GPIO11: J2.18, U2.18 (CMD)
/GPIO16: J1.12, U2.27 (GPIO16)
/GPIO23: J1.2, U2.37 (GPIO23)
/PCA_A0: JP1.2 (B), R4.2, U1.1 (A0)
/PCA_A1: JP2.2 (B), R6.2, U1.2 (A1)
/PCA_A2: JP3.2 (B), R7.2, U1.3 (A2)
/PCA_A3: JP4.2 (B), R9.2, U1.4 (A3)
/PCA_A4: JP5.2 (B), R11.2, U1.5 (A4)
/PCA_A5: JP6.2 (B), R12.2, U1.24 (A5)
/PCA_A6: JP7.2 (B), R29.2, U1.25 (A6)
/PWR_LED_1: D7.2 (A), R14.2
/PWR_LED_2: D6.2 (A), R13.2
/RX0: J1.5, J8.2, U2.34 (U0RXD/GPIO3)
/SCL1: J1.16, J7.2, R32.1, U2.23 (MTDO/GPIO15/ADC2_CH3)
/SDA1: J2.15, J7.3, R33.1, U2.15 (MTCK/GPIO13/ADC2_CH4)
/TX0: J1.4, J8.3, U2.35 (U0TXD/GPIO1)
/VS_UNSAFE: D5.2 (A), D10.2 (A), J3.1, J4.2
/buck2/BUCK_VIN: SW1.2; also elsewhere on the board
/buck2/VOUT: C28.1, J5.1 (VBUS), R13.1; also elsewhere on the board
FSYNC: J2.7, J16.1, U2.7 (32K_XP/GPIO32/ADC1_CH4)
GND: C1.2, C26.2, C27.2, C28.2, C29.2, C30.1, D1.1 (K), D2.1 (K), D3.1 (K), D4.1 (K), D6.1 (K), D7.1 (K), H1.1, H2.1, H3.1, H4.1, J1.1, J1.7, J2.14, J3.2, J3.3 (MountPin), J4.1, J5.4 (GND), J5.5 (Shield), J6.1, J7.1, J8.1, J13.1, J14.1, J15.1, J16.9, J18.1, R4.1, R6.1, R7.1, R9.1, R10.2, R11.1, R12.1, R29.1, R30.2, U1.14 (VSS), U2.14 (GND), U2.32 (GND), U2.38 (GND), U13.1 (GND); also elsewhere on the board
INT: J2.8, J16.3, U2.8 (32K_XN/GPIO33/ADC1_CH5)
M_OE: J1.13, R31.1, U1.23 (~OE), U2.26 (ADC2_CH0/GPIO4)
SCL0: J1.3, J16.8, J18.2, R15.1, U1.26 (SCL), U2.36 (GPIO22)
SDA0: J1.6, J16.7, J18.3, R16.1, U1.27 (SDA), U2.33 (GPIO21)
VBATT: J2.9, J17.2, R8.2, U2.9 (DAC_1/ADC2_CH8/GPIO25)
VS: D5.1 (K), D10.1 (K), R8.1, SW1.1; also elsewhere on the board
VSS: C26.1, C29.1, J2.19, U2.19 (5V), U13.3 (VI); also elsewhere on the board

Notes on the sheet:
The PCA driver has an active-low enable, so we pull-up to 3.3 V (high) to prevent accidental activation.
PCA9635 datasheet: https://www.nxp.com/docs/en/data-sheet/PCA9635.pdf
Find chosen pinouts in the README: https://github.com/eccentricOrange/int-brain/blob/ main/README.md
NCS
Motor Logic Section
AD0
SBC Power section
Note that this +3.3VA is different from the +3.3V used in the rest of the circuit. This is to ensure that the 3.3 V required for the ESP32 is left undisturbed and other components are powered using a dedicated AMS1117-3.3 LDO.
Sensor Module product links - https://robu.in/product/gy-9255-mpu9255-sensor-module/ - https://www.electronicscomp.com/mpu9250-9-axis-gyro- accelerometer-module - https://www.amazon.in/Electrobot-MPU9250-Accelerator- Magnetometer-Arduino/dp/B08R3SXRVH - https://roboticsdna.in/product/gy-87-mpu-9265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
Support for quadrature rotary encoders is added, in case a compatible motor with encoders can be found. These are connected directly to the ESP32 microcontroller (instead of using another PCA PWM driver) to provide easy configration of hardware interrupts in case this approach is used when programm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
Drive all motors using PWM signals, sent from the ESP32 using I2C. Eachmotor requires two PWM lines, each corresponding to one pair of the MOSFETs in the H-bridge motor driver. An additional PWM pin has been allocated per motor to indicate speed with LED brightness.
MPU9250 Datasheet: https://invensense.tdk.com/wp-content/uploads/2015/02/ PS-MPU-9250A-01-v1.1.pdf
Take in 12 V or 24 V (approx; for most calculations, peak values assuming lithium-polymer cells at 4.2 V are considered). Provide basic reverse-polarity protection (diodes) and also reduce to 5V for most of the board's functionality. Provide a voltage reading corresponding to the battery leverl for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
EDA
Symbol and footprint libraries: https://github.com/espressif/kicad-libraries
Use a potential divider to reduce the battery voltage. For various Li-Po batteries, we assume 4.2 V per cell (at full charge). We expect about 3.12 mW - 12.96 mW to be dissipated here. 3S: 47k and 3.9k --> 0.9654223 V 6S: 47k and 2k --> 1.028571429 V The ESP32 seems to read realiably up to around 1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
ECL
Protocol pins (I2C0 and UART0) are chosen to keep compliance with the Arduino framework, even though this is unlikely to be used with this board. Most other GPIO are chosen based on physical proximity to peripherals and ease of routing the PCB.
ESP32 Microcontroller
Provide up to 5V 5A at a USB port, used to drive an SBC such as the Raspberry Pi 5B
Pinout and other information: https://docs.espressif.com/projects/esp-idf/en/stable/esp32/ hw-reference/esp32/get-started-devkitc.html
Distriute functionality from the ESP32 to the rest of the board. In general, the signal bus is used to connect headers on either side of the board to access its GPIO and other functionality. Nothing else on the board depends on ESP32 3.3V, so this can be used for peripherals.
These ADC pins can only handle input, so they are used for current-sense voltage drops.
3.3V LDO
I2C address selection is done by pulling down all bits to 0 using a 10k resistor to ground. To make any of them 1, the corresponding solder joint can be filled, and they'll be shorted to 3.3 V.
A second I2C port is needed to allow the ESP32 to act as a slave to another SBC such as a Raspberry Pi or an NVIDIA Jetson.
Power Input Section
MPU9250 IMU

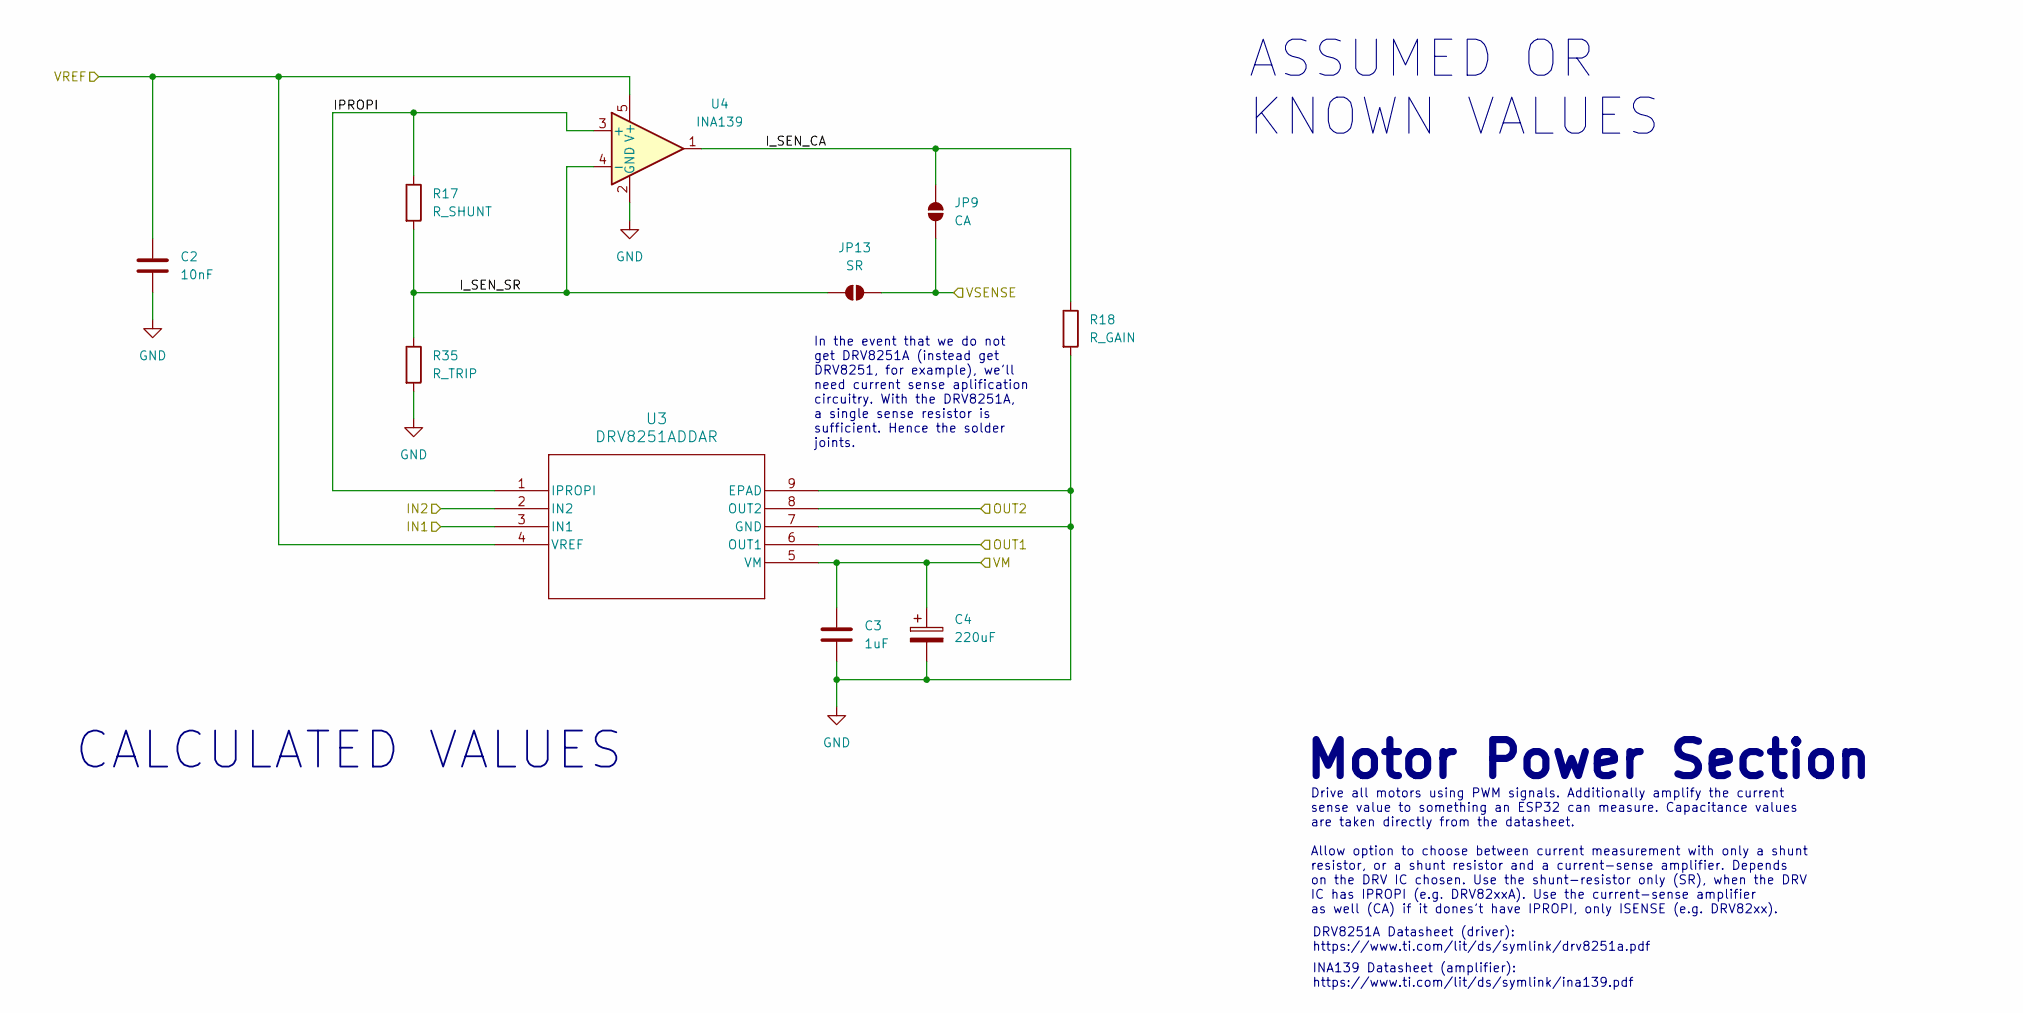
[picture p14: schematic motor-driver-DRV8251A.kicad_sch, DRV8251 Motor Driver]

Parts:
C2: 10nF; C_0805_2012Metric_Pad1.18x1.45mm_HandSolder
C3: 1uF; C_0805_2012Metric_Pad1.18x1.45mm_HandSolder
C4: 220uF; CP_Elec_8x10.5
JP9: CA; SolderJumper-2_P1.3mm_Open_Pad1.0x1.5mm
JP13: SR; SolderJumper-2_P1.3mm_Open_Pad1.0x1.5mm
R17: R_SHUNT; R_2512_6332Metric_Pad1.40x3.35mm_HandSolder
R18: R_GAIN; R_1206_3216Metric_Pad1.30x1.75mm_HandSolder
R35: R_TRIP; R_1206_3216Metric_Pad1.30x1.75mm_HandSolder
U3: DRV8251ADDAR; SOIC-8-1EP_3.9x4.9mm_P1.27mm_EP2.29x3mm_ThermalVias
U4: INA139; SOT-23-5_HandSoldering

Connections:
1MB_SENSE: JP9.1 (A), JP13.2 (B); also elsewhere on the board
+3.3V: C2.1, U3.4 (VREF), U4.5 (V+); also elsewhere on the board
/1MB1: U3.6 (OUT1); also elsewhere on the board
/1MB2: U3.8 (OUT2); also elsewhere on the board
/1MB_IN1: U3.3 (IN1); also elsewhere on the board
/1MB_IN2: U3.2 (IN2); also elsewhere on the board
/motor-driver-2/IPROPI: R17.1, U3.1 (IPROPI), U4.3 (+)
/motor-driver-2/I_SEN_CA: JP9.2 (B), R18.1, U4.1
/motor-driver-2/I_SEN_SR: JP13.1 (A), R17.2, R35.1, U4.4 (-)
GND: C2.2, C3.2, C4.2, R18.2, R35.2, U3.7 (GND), U3.9 (EPAD), U4.2 (GND); also elsewhere on the board
VS: C3.1, C4.1, U3.5 (VM); also elsewhere on the board

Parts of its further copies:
C5, C12, C19: 10nF; C_0805_2012Metric_Pad1.18x1.45mm_HandSolder
C6, C13, C20: 1uF; C_0805_2012Metric_Pad1.18x1.45mm_HandSolder
C7, C14, C21: 220uF; CP_Elec_8x10.5
JP8, JP10, JP11: CA; SolderJumper-2_P1.3mm_Open_Pad1.0x1.5mm
JP12, JP14, JP15: SR; SolderJumper-2_P1.3mm_Open_Pad1.0x1.5mm
R19, R23, R27: R_SHUNT; R_2512_6332Metric_Pad1.40x3.35mm_HandSolder
R20, R24, R28: R_GAIN; R_1206_3216Metric_Pad1.30x1.75mm_HandSolder
R34, R36, R37: R_TRIP; R_1206_3216Metric_Pad1.30x1.75mm_HandSolder
U5, U8, U11: DRV8251ADDAR; SOIC-8-1EP_3.9x4.9mm_P1.27mm_EP2.29x3mm_ThermalVias
U6, U9, U12: INA139; SOT-23-5_HandSoldering

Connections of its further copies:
1MA_SENSE: JP8.1 (A), JP12.2 (B); also elsewhere on the board
2MA_SENSE: JP10.1 (A), JP14.2 (B); also elsewhere on the board
2MB_SENSE: JP11.1 (A), JP15.2 (B); also elsewhere on the board
+3.3V: C5.1, C12.1, C19.1, U5.4 (VREF), U6.5 (V+), U8.4 (VREF), U9.5 (V+), U11.4 (VREF), U12.5 (V+); also elsewhere on the board
/1MA1: U8.6 (OUT1); also elsewhere on the board
/1MA2: U8.8 (OUT2); also elsewhere on the board
/1MA_IN1: U8.3 (IN1); also elsewhere on the board
/1MA_IN2: U8.2 (IN2); also elsewhere on the board
/2MA1: U5.6 (OUT1); also elsewhere on the board
/2MA2: U5.8 (OUT2); also elsewhere on the board
/2MA_IN1: U5.3 (IN1); also elsewhere on the board
/2MA_IN2: U5.2 (IN2); also elsewhere on the board
/2MB1: U11.6 (OUT1); also elsewhere on the board
/2MB2: U11.8 (OUT2); also elsewhere on the board
/2MB_IN1: U11.3 (IN1); also elsewhere on the board
/2MB_IN2: U11.2 (IN2); also elsewhere on the board
/motor-driver-1/IPROPI: R23.1, U8.1 (IPROPI), U9.3 (+)
/motor-driver-1/I_SEN_CA: JP8.2 (B), R24.1, U9.1
/motor-driver-1/I_SEN_SR: JP12.1 (A), R23.2, R34.1, U9.4 (-)
/motor-driver-3/IPROPI: R19.1, U5.1 (IPROPI), U6.3 (+)
/motor-driver-3/I_SEN_CA: JP10.2 (B), R20.1, U6.1
/motor-driver-3/I_SEN_SR: JP14.1 (A), R19.2, R36.1, U6.4 (-)
/motor-driver-4/IPROPI: R27.1, U11.1 (IPROPI), U12.3 (+)
/motor-driver-4/I_SEN_CA: JP11.2 (B), R28.1, U12.1
/motor-driver-4/I_SEN_SR: JP15.1 (A), R27.2, R37.1, U12.4 (-)
GND: C5.2, C6.2, C7.2, C12.2, C13.2, C14.2, C19.2, C20.2, C21.2, R20.2, R24.2, R28.2, R34.2, R36.2, R37.2, U5.7 (GND), U5.9 (EPAD), U6.2 (GND), U8.7 (GND), U8.9 (EPAD), U9.2 (GND), U11.7 (GND), U11.9 (EPAD), U12.2 (GND); also elsewhere on the board
VS: C6.1, C7.1, C13.1, C14.1, C20.1, C21.1, U5.5 (VM), U8.5 (VM), U11.5 (VM); also elsewhere on the board

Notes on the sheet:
In the event that we do not get DRV8251A (instead get DRV8251, for example), we'll need current sense aplification circuitry. With the DRV8251A, a single sense resistor is sufficient. Hence the solder joints.
CALCULATED VALUES
Motor Power Section
DRV8251A Datasheet (driver): https://www.ti.com/lit/ds/symlink/drv8251a.pdf
INA139 Datasheet (amplifier): https://www.ti.com/lit/ds/symlink/ina139.pdf
Drive all motors using PWM signals. Additionally amplify the current sense value to something an ESP32 can measure. Capacitance values are taken directly from the datasheet. Allow option to choose between current measurement with only a shunt resistor, or a shunt resistor and a current-sense amplif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
ASSUMED OR KNOWN VALUES

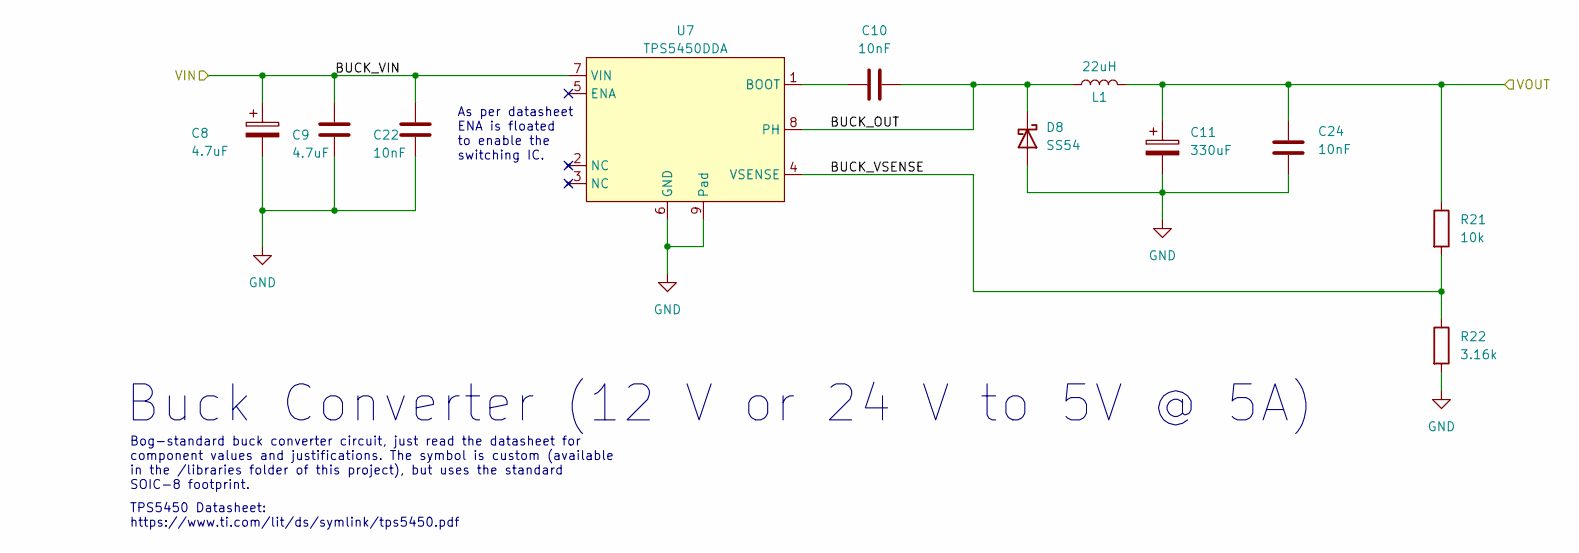
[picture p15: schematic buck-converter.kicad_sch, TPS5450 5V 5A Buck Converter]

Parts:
C8: 4.7uF; CP_Elec_4x5.4
C9: 4.7uF; C_0805_2012Metric_Pad1.18x1.45mm_HandSolder
C10, C22, C24: 10nF; C_0805_2012Metric_Pad1.18x1.45mm_HandSolder
C11: 330uF; CP_Elec_8x10.5
D8: SS54; D_SMA_Handsoldering
L1: 22uH; L_10.4x10.4_H4.8
R21: 10k; R_1206_3216Metric_Pad1.30x1.75mm_HandSolder
R22: 3.16k; R_1206_3216Metric_Pad1.30x1.75mm_HandSolder
U7: TPS5450DDA; SOIC-8-1EP_3.9x4.9mm_P1.27mm_EP2.29x3mm_ThermalVias

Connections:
/buck1/BUCK_OUT: C10.2, D8.1 (K), L1.1, U7.8 (PH)
/buck1/BUCK_VSENSE: R21.2, R22.1, U7.4 (VSENSE)
GND: C8.2, C9.2, C11.2, C22.2, C24.2, D8.2 (A), R22.2, U7.6 (GND), U7.9 (Pad); also elsewhere on the board
unnamed: C10.1, U7.1 (BOOT)
VS: C8.1, C9.1, C22.1, U7.7 (VIN); also elsewhere on the board
VSS: C11.1, C24.1, L1.2, R21.1; also elsewhere on the board

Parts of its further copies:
C15: 4.7uF; CP_Elec_4x5.4
C16: 4.7uF; C_0805_2012Metric_Pad1.18x1.45mm_HandSolder
C17, C23, C25: 10nF; C_0805_2012Metric_Pad1.18x1.45mm_HandSolder
C18: 330uF; CP_Elec_8x10.5
D9: SS54; D_SMA_Handsoldering
L2: 22uH; L_10.4x10.4_H4.8
R25: 10k; R_1206_3216Metric_Pad1.30x1.75mm_HandSolder
R26: 3.16k; R_1206_3216Metric_Pad1.30x1.75mm_HandSolder
U10: TPS5450DDA; SOIC-8-1EP_3.9x4.9mm_P1.27mm_EP2.29x3mm_ThermalVias

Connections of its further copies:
/buck2/BUCK_OUT: C17.2, D9.1 (K), L2.1, U10.8 (PH)
/buck2/BUCK_VIN: C15.1, C16.1, C23.1, U10.7 (VIN); also elsewhere on the board
/buck2/BUCK_VSENSE: R25.2, R26.1, U10.4 (VSENSE)
/buck2/VOUT: C18.1, C25.1, L2.2, R25.1; also elsewhere on the board
GND: C15.2, C16.2, C18.2, C23.2, C25.2, D9.2 (A), R26.2, U10.6 (GND), U10.9 (Pad); also elsewhere on the board
unnamed: C17.1, U10.1 (BOOT)

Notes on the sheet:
Buck Converter (12 V or 24 V to 5V @ 5A)
TPS5450 Datasheet: https://www.ti.com/lit/ds/symlink/tps5450.pdf
Bog-standard buck converter circuit, just read the datasheet for component values and justifications. The symbol is custom (available in the /libraries folder of this project), but uses the standard SOIC-8 footprint.
As per datasheet ENA is floated to enable the switching IC.

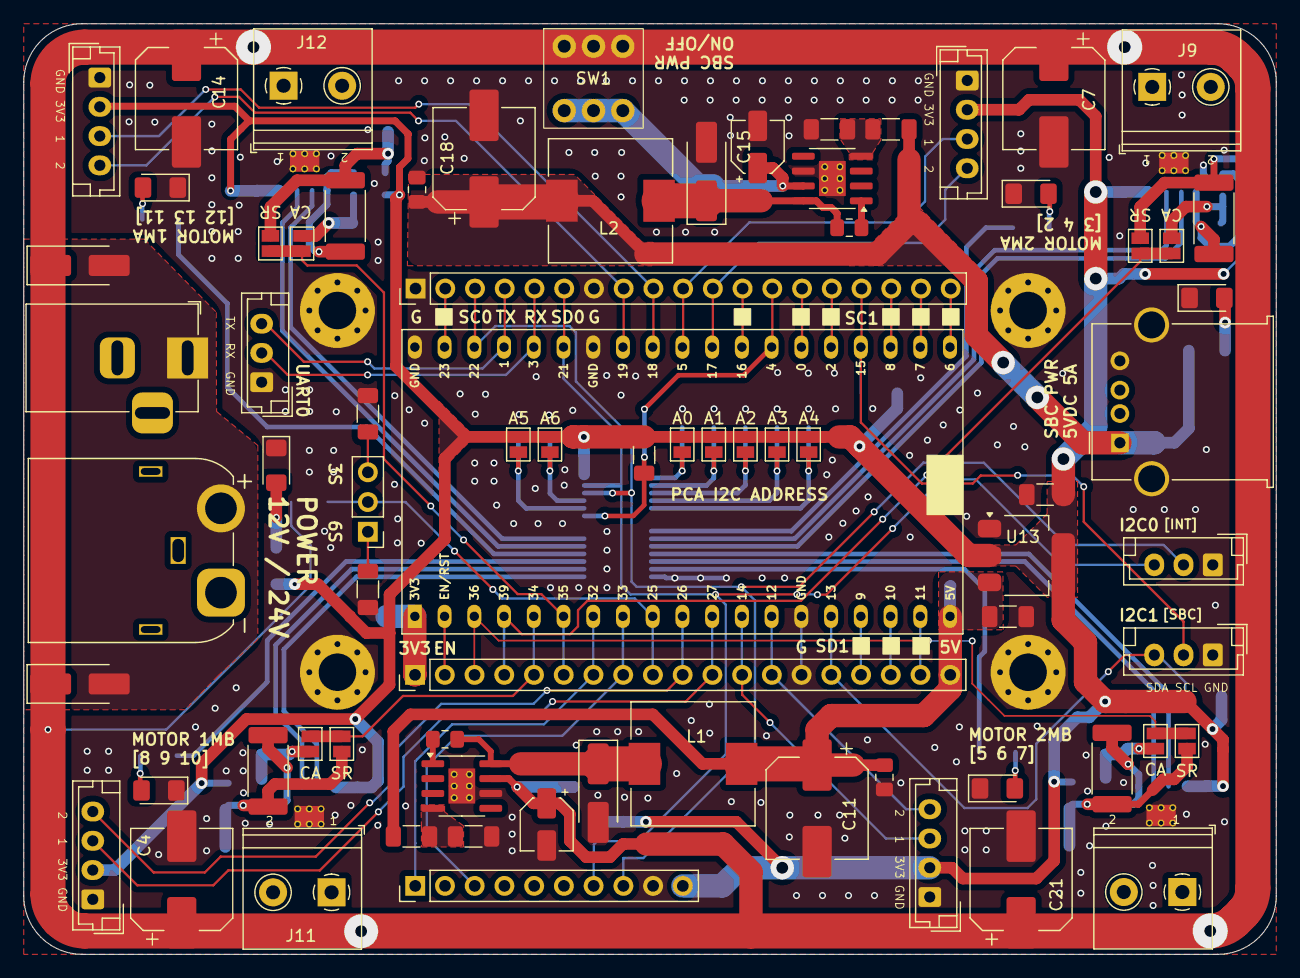
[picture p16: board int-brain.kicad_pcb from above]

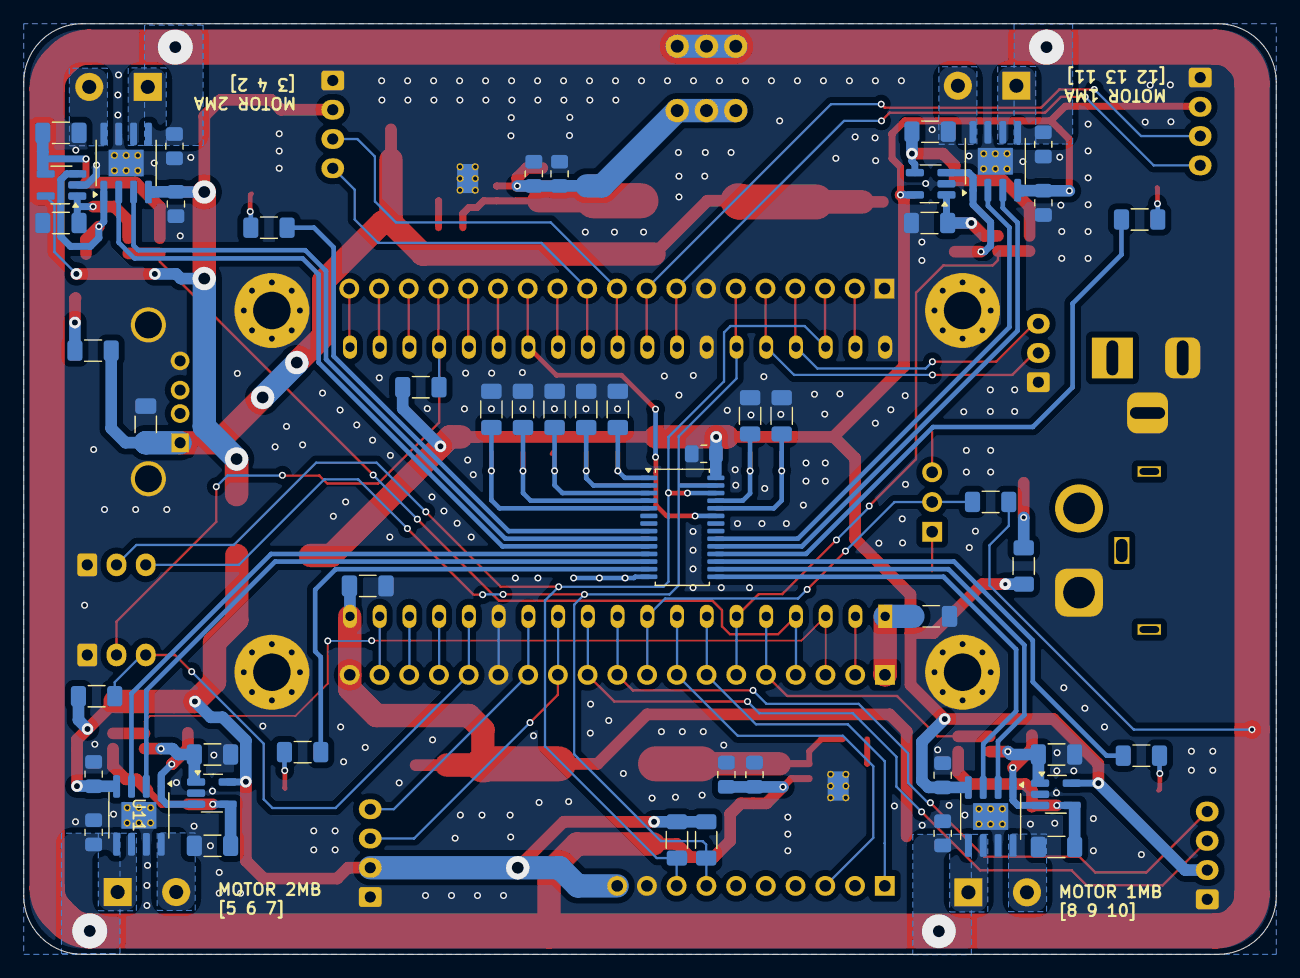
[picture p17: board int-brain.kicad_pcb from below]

Board: 2 copper layers, 107.0 x 79.5 mm, 130 parts (51 on the bottom side), 94 nets.

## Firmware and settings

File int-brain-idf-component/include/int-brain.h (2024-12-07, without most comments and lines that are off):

#pragma once
#include <string.h>
#include "driver/gpio.h"
#include "driver/i2c_master.h"
#include "driver/i2c_slave.h"
#include "driver/pulse_cnt.h"
#include "driver/uart.h"
#include "esp_adc/adc_cali.h"
#include "esp_adc/adc_cali_scheme.h"
#include "esp_adc/adc_oneshot.h"
#include "esp_err.h"
#include "esp_log.h"
#include "esp_task.h"
#include "esp_timer.h"
#include "freertos/queue.h"
#include "int-brain-sbc-registers.h"
#define NUMBER_OF_MOTORS 4
extern const uint8_t PCA_DRIVER_ADDRESS;
extern const int ENCODER_CPR;  // pulses
#define DEFAULT_ENCODER_CPR 1024  // pulses
extern const int MOTOR_GEAR_RATIO;
#define DEFAULT_MOTOR_GEAR_RATIO 1
extern const int MAX_MOTOR_RPM;
#define DEFAULT_MAX_MOTOR_RPM 80
extern const int ENCODER_LIMIT;  // pulses
#define DEFAULT_ENCODER_LIMIT ENCODER_CPR * MOTOR_GEAR_RATIO  // pulses
extern const int ENCODER_GLITCH_PERIOD;  // ns
#define DEFAULT_ENCODER_GLITCH_PERIOD 1e3  // ns
#define ADC_CHOSEN_ATTEN ADC_ATTEN_DB_0
#define ADC_CHHOSEN_BITWIDTH ADC_BITWIDTH_DEFAULT
#define MOTOR_MAXIMUM_STALL_CURRENT 750
#define MOTOR_MINIMUM_DISCONNECT_PWM 50
#define MOTOR_MINIMUM_CONNECTED_CURRENT 100
#define MOTOR_STOPPED_CURRENT 75
#define I2C_STANDARD_TIMEOUT_MS 3e3
struct motor_t {
    uint8_t output_pin_1;
    uint8_t output_pin_2;
    uint8_t encoder_pin_1;
    uint8_t encoder_pin_2;
    uint8_t LED_pin;
    uint8_t current_sense_pin;
    pcnt_unit_handle_t encoder_unit_handle;
} typedef motor_t;
enum motor_direction_t {
    IDLE = 0b00,
    FORWARD = 0b01,
    REVERSE = 0b10,
    BRAKE = 0b11,
} typedef motor_direction_t;
enum motor_safety_mode_t {
    UNSAFE = 0b00,
    PROTECT_STALL = 0b01,
    PROTECT_DISCONNECT = 0b10,
    PROTECT_STALL_AND_DISCONNECT = 0b11,
} typedef motor_safety_mode_t;
enum motor_speed_mode_t {
    STOP = 0b00,
    MAX = 0b01,
    COMMAND = 0b10,
    COMMON = 0b11,
} typedef motor_speed_mode_t;
enum bot_direction_t {
    FRONT = 0,
    BACK = 1,
    ROTATE_CLOCKWISE = 2,
    ROTATE_COUNTERCLOCKWISE = 3,
    FRONT_LEFT = 4,
    FRONT_RIGHT = 5,
    BACK_LEFT = 6,
    BACK_RIGHT = 7,
} typedef bot_direction_t;
static motor_t DEFAULT_MOTORS_PIN_OUTS[NUMBER_OF_MOTORS] = {
    {
        .LED_pin = 11,
        .output_pin_1 = 12,
        .output_pin_2 = 13,
        .encoder_pin_1 = 18,
        .encoder_pin_2 = 19,
        .current_sense_pin = 35,
    },
    {
        .LED_pin = 10,
        .output_pin_1 = 8,
        .output_pin_2 = 9,
        .encoder_pin_1 = 23,
        .encoder_pin_2 = 25,
        .current_sense_pin = 34,
    },
    {
        .LED_pin = 2,
        .output_pin_1 = 3,
        .output_pin_2 = 4,
        .encoder_pin_1 = 5,
        .encoder_pin_2 = 17,
        .current_sense_pin = 39,
    },
    {
        .LED_pin = 7,
        .output_pin_1 = 5,
        .output_pin_2 = 6,
        .encoder_pin_1 = 14,
        .encoder_pin_2 = 12,
        .current_sense_pin = 36,
    }};
#define PCA_MOTOR_ENABLE_PIN 4
#define DEFAULT_LED_PIN 2
#define I2C0_MASTER_SCL_PIN 22
#define I2C0_MASTER_SDA_PIN 21
#define I2C1_SLAVE_SCL_PIN 15
#define I2C1_SLAVE_SDA_PIN 13
#define DEFAULT_UART0_TX_PIN 1
#define DEFAULT_UART0_RX_PIN 3
#define UART_CHOSEN_PORT UART_NUM_0
#define BATTERY_VOLTAGE_SENSE_PIN 25
#define ESP32_I2C1_SLAVE_ADDRESS 0x30
#define PCA_DRIVER_I2C0_DEFAULT_ADDRESS 0x40
#define IMU_MPU9250_I2C0_DEFAULT_ADDRESS 0x68
#define PCA_I2C0_SPEED 100e3
#define PCA_I2C0_WRITE_TIMEOUT 50
#define MAX_INT_SIZE sizeof(int)
#define SBC_I2C1_RECEIVE_MAX_DATA_LENGTH 8
#define SBC_I2C1_RECEIVE_DATA_BUFFER_SIZE (SBC_I2C1_RECEIVE_MAX_DATA_LENGTH + 1)  // +1 for the command byte
#define SBC_I2C1_SEND_MAX_DATA_LENGTH (NUMBER_OF_MOTORS * MAX_INT_SIZE)
#define SBC_I2C1_SEND_DATA_BUFFER_SIZE (SBC_I2C1_SEND_MAX_DATA_LENGTH)
static const i2c_master_bus_config_t DEFAULT_I2C0_MASTER_CONFIG = {
    .clk_source = I2C_CLK_SRC_DEFAULT,
    .i2c_port = I2C_NUM_0,
    .sda_io_num = I2C0_MASTER_SDA_PIN,
    .scl_io_num = I2C0_MASTER_SCL_PIN,
    .glitch_ignore_cnt = 7,
    .flags.enable_internal_pullup = false,  // We have external pull-ups
};
static const i2c_slave_config_t DEFAULT_I2C1_SLAVE_CONFIG = {
    .addr_bit_len = I2C_ADDR_BIT_7,
    .clk_source = I2S_CLK_SRC_DEFAULT,
    .i2c_port = I2C_NUM_1,
    .send_buf_depth = 256,
    .sda_io_num = I2C1_SLAVE_SDA_PIN,
    .scl_io_num = I2C1_SLAVE_SCL_PIN,
    .slave_addr = ESP32_I2C1_SLAVE_ADDRESS,
};
#define UART0_RX_BUFFER_SIZE 1024
#define UART0_TX_BUFFER_SIZE 1024
static const uart_config_t DEFAULT_UART0_CONFIG = {
    .baud_rate = 115200,
    .data_bits = UART_DATA_8_BITS,
    .parity = UART_PARITY_DISABLE,
    .stop_bits = UART_STOP_BITS_1,
    .flow_ctrl = UART_HW_FLOWCTRL_DISABLE,
    .rx_flow_ctrl_thresh = 122,
};
#define PCA_MODE1_ADDRESS 0x00
#define PCA_MODE1 0b10000001
#define PCA_LED_DRIVER_ADDRESS 0x14
#define PCA_ENABLE_DRIVERS 0b10101010
#define PWM0_REGISTER_ADDRESS 0x02
#define PCA_NUMBER_OF_LED_DRIVERS 4
#define PCA_MAX_PWM_DUTY 255
#define PCA_MAX_LED_PWM 155
extern bool sbc_data_received_flag;
extern uint8_t sbc_i2c1_receive_buffer[SBC_I2C1_RECEIVE_DATA_BUFFER_SIZE];
extern uint8_t sbc_i2c1_send_buffer[SBC_I2C1_SEND_DATA_BUFFER_SIZE];
extern char sbc_uart0_receive_buffer[UART0_RX_BUFFER_SIZE];
extern char sbc_uart0_send_buffer[UART0_TX_BUFFER_SIZE];
extern size_t uart_received_data_length;
extern int _encoder_positions[NUMBER_OF_MOTORS];
extern int _encoder_positions_previous[NUMBER_OF_MOTORS];
extern int _motor_rpms[NUMBER_OF_MOTORS];
extern int _motor_currents[NUMBER_OF_MOTORS];
extern uint64_t _previous_timer_value;
extern uint8_t _motor_stall_status;
extern uint8_t _motor_disconnect_status;
extern uint8_t _motor_mode_register;
extern uint8_t _motor_direction_register;
extern uint8_t _raw_motor_speeds[NUMBER_OF_MOTORS];
extern uint8_t _filtered_motor_speeds[NUMBER_OF_MOTORS];
extern motor_direction_t _motor_directions[NUMBER_OF_MOTORS];
extern motor_safety_mode_t _motor_safety_mode;
extern motor_speed_mode_t _motor_speed_mode;
extern bool _motor_output_enabled;
extern bot_direction_t _bot_direction;
extern uint8_t _common_speed;
extern int _battery_voltage;
extern i2c_master_dev_handle_t _PCA_I2C0_device_handle;
extern adc_oneshot_unit_handle_t _adc1_unit_handle;
extern adc_cali_handle_t _adc1_cali_handle;
extern adc_oneshot_unit_handle_t _adc2_unit_handle;
extern adc_cali_handle_t _adc2_cali_handle;
extern esp_err_t PCA_init(i2c_master_bus_handle_t bus_handle);  // direct task function
extern esp_err_t _PCA_add_driver_to_I2C0(i2c_master_bus_handle_t bus_handle);  // direct task function
extern esp_err_t _PCA_set_register(uint8_t register_address, uint8_t data);    // direct task function
extern esp_err_t _PCA_enable_internal_drivers();                               // direct task function
extern esp_err_t _PCA_MOE_init();                                              // direct task function
extern esp_err_t PCA_command_LED(motor_t motor, uint8_t PWM);                                          // direct task function
extern esp_err_t PCA_command_motor(motor_t motor, motor_direction_t direction, uint8_t PWM);           // direct task function
extern esp_err_t PCA_command_motor_with_LED(motor_t motor, motor_direction_t direction, uint8_t PWM);  // direct task function
extern void direction_to_PWMs(motor_direction_t direction, uint8_t PWM_in, uint8_t* PWM_1_out, uint8_t* PWM_2_out);  // direct task function
extern uint8_t motor_PWM_mode_filter(uint8_t command_PWM, uint8_t common_speed, motor_speed_mode_t speed_mode);      // direct task function
extern esp_err_t set_motor_mode_register(motor_safety_mode_t safety_mode, motor_speed_mode_t speed_mode, bool enable);  // pseudo register-based function
extern esp_err_t set_motor_safety_mode(motor_safety_mode_t safety_mode);                                                // pseudo register-based function
extern esp_err_t set_motor_speed_mode(motor_speed_mode_t speed_mode);                                                   // pseudo register-based function
extern esp_err_t enable_motor_output();                                                                                 // pseudo register-based function
extern esp_err_t disable_motor_output();                                                                                // pseudo register-based function
extern esp_err_t set_motor_speeds(uint8_t* speeds);                    // pseudo register-based function
extern esp_err_t set_common_motor_speed(uint8_t speed);                // pseudo register-based function
extern esp_err_t set_motor_directions(motor_direction_t* directions);  // pseudo register-based function
extern esp_err_t set_bot_direction(bot_direction_t direction);         // pseudo register-based function
extern esp_err_t publish_motor_command(motor_t* motors);  // pseudo register-based function
extern esp_err_t update_motor_disconnect_status();        // pseudo register-based function
extern esp_err_t ADC1_motors_init(motor_t* motors, size_t number_of_motors);               // direct task function
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

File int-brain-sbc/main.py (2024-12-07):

import time

import serial
import smbus2

import int_brain_sbc

DELAY = 1e-3

with serial.Serial("/dev/serial0", baudrate=115200, timeout=1) as port:
# with smbus2.SMBus(1) as port:

    bot = int_brain_sbc.IntBrain(port, 0x30)

    bot.all_motors.set_motor_mode(
        safety_mode=int_brain_sbc.enums.MotorSafetyMode.UNSAFE,
        speed_mode=int_brain_sbc.enums.MotorSpeedMode.COMMAND_SPEED,
        enable=True
    )
    time.sleep(DELAY)

    bot.bot.set_robot_direction(direction=int_brain_sbc.enums.BotDirections.FRONT)
    time.sleep(DELAY)

    for motor_index in range(int_brain_sbc.enums.BotQueriesLimits.NUMBER_OF_MOTORS.value):
        bot.individual_motor.set_speed(0, motor_index)
        time.sleep(DELAY)

    try:
        while(1):
            for motor_index in range(int_brain_sbc.enums.BotQueriesLimits.NUMBER_OF_MOTORS.value):
                for duty_cycle in range(int_brain_sbc.enums.BotQueriesLimits.MAX_PWM.value + 1):
                    bot.individual_motor.set_speed(duty_cycle, motor_index)
                    time.sleep(DELAY)
                    print(f"[{motor_index}][{duty_cycle:03}] Currents: {bot.all_motors.get_motor_current()}, Encoder: {bot.all_motors.get_encoder_data()}, Speeds: {bot.all_motors.get_speeds()}, Battery level: {bot.bot.get_battery_voltage()}")

                for duty_cycle in range(int_brain_sbc.enums.BotQueriesLimits.MAX_PWM.value, -1, -1):
                    bot.individual_motor.set_speed(duty_cycle, motor_index)
                    time.sleep(DELAY)
                    print(f"[{motor_index}][{duty_cycle:03}] Currents: {bot.all_motors.get_motor_current()}, Encoder: {bot.all_motors.get_encoder_data()}, Speeds: {bot.all_motors.get_speeds()}, Battery level: {bot.bot.get_battery_voltage()}")

    except KeyboardInterrupt:
        for motor_index in range(int_brain_sbc.enums.BotQueriesLimits.NUMBER_OF_MOTORS.value):
            bot.individual_motor.set_speed(0, motor_index)
            time.sleep(DELAY)

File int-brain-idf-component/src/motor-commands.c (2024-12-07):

#include "int-brain.h"

/** @file motor-commands.c
 *  @brief Implement the functions to control the motors.
 *  @author @eccentricOrange
 */

/** @brief Convert the `motor_direction_t` style direction and the PWM for a motor into PWM values for each terminal of the motor.
 *  @attention Direct task function
 *  @param direction Direction to move the motor.
 *  @param PWM_in PWM value for the motor.
 *  @param PWM_1_out Pointer to the PWM value for terminal 1.
 *  @param PWM_2_out Pointer to the PWM value for terminal 2.
 */
void direction_to_PWMs(motor_direction_t direction, uint8_t PWM_in, uint8_t* PWM_1_out, uint8_t* PWM_2_out) {
    switch (direction) {
        // Idle
        case IDLE:
            *PWM_1_out = 0;
            *PWM_2_out = 0;
            break;

        // Reverse
        case REVERSE:
            *PWM_1_out = 0;
            *PWM_2_out = PWM_in;
            break;

        // Brake
        case BRAKE:
            *PWM_1_out = 0;
            *PWM_2_out = 0;
            break;

        // Forward
        case FORWARD:
            *PWM_1_out = PWM_in;
            *PWM_2_out = 0;
            break;

        // Error, brake and exit
        default:
            *PWM_1_out = 0;
            *PWM_2_out = 0;
            break;
    }

    return;
}

/** @brief Choose the PWM value based on the motor mode as defined in `motor_speed_mode_t`.
 *  @attention Direct task function
 *  @param command_PWM Per-motor command PWM
 *  @param common_speed Common PWM speed for all motors
 *  @param speed_mode Speed mode
 *  @return Chosen PWM value.
 */
uint8_t motor_PWM_mode_filter(uint8_t command_PWM, uint8_t common_speed, motor_speed_mode_t speed_mode) {
    switch (speed_mode) {
        case STOP:
            return 0;

        case MAX:
            return PCA_MAX_PWM_DUTY;

        case COMMAND:
            return command_PWM;

        case COMMON:
            return common_speed;

        default:
            return command_PWM;
    }
}

/** @brief Update the motor mode register `_motor_mode_register` and the motor mode variables.
 *  @attention Pseudo-register task function
 *  @param safety_mode Safety mode
 *  @param speed_mode Speed mode
 *  @param enable Enable motor output?
 *  @return `ESP_OK` if successful.
 */
esp_err_t set_motor_mode_register(motor_safety_mode_t safety_mode, motor_speed_mode_t speed_mode, bool enable) {
    _motor_mode_register = 0;

    _motor_mode_register |= safety_mode << MOTOR_MODE_SAFETY_BIT_0_POSITION;
    _motor_mode_register |= speed_mode << MOTOR_MODE_SPEED_BIT_0_POSITION;
    _motor_mode_register |= enable << MOTOR_MODE_ENABLE_BIT_POSITION;

    _motor_safety_mode = safety_mode;
    _motor_speed_mode = speed_mode;
    _motor_output_enabled = enable;

    return ESP_OK;
}

/** @brief Update the motor safety mode register `_motor_safety_mode` and the motor mode variables.
 *  @attention Pseudo-register task function
 *  @param safety_mode Safety mode
 *  @return `ESP_OK` if successful.
 */
esp_err_t set_motor_safety_mode(motor_safety_mode_t safety_mode) {
    _motor_safety_mode = safety_mode;
    return set_motor_mode_register(_motor_safety_mode, _motor_speed_mode, _motor_output_enabled);
}

/** @brief Update the motor speed mode register `_motor_speed_mode` and the motor mode variables.
 *  @attention Pseudo-register task function
 *  @param speed_mode Speed mode
 *  @return `ESP_OK` if successful.
 */
esp_err_t set_motor_speed_mode(motor_speed_mode_t speed_mode) {
    _motor_speed_mode = speed_mode;
    return set_motor_mode_register(_motor_safety_mode, _motor_speed_mode, _motor_output_enabled);
}

/** @brief Update the motor output register `_motor_output_enabled` and the motor mode variables. Sets it to true.
 *  @attention Pseudo-register task function
 *  @return `ESP_OK` if successful.
 */
esp_err_t enable_motor_output() {
    _motor_output_enabled = true;
    return set_motor_mode_register(_motor_safety_mode, _motor_speed_mode, _motor_output_enabled);
}

/** @brief Update the motor output register `_motor_output_enabled` and the motor mode variables. Sets it to false.
 *  @attention Pseudo-register task function
 *  @return `ESP_OK` if successful.
 */
esp_err_t disable_motor_output() {
    _motor_output_enabled = false;
    return set_motor_mode_register(_motor_safety_mode, _motor_speed_mode, _motor_output_enabled);
}

/** @brief Update the motor speeds `_raw_motor_speeds` pseudo-register.
 *  @attention Pseudo-register task function
 *  @param speeds Array of motor speeds.
 *  @return `ESP_OK` if successful.
 */
esp_err_t set_motor_speeds(uint8_t* speeds) {
    for (size_t i = 0; i < NUMBER_OF_MOTORS; i++) {
        _raw_motor_speeds[i] = speeds[i];
    }

    return ESP_OK;
}

/** @brief Update the common motor speed `_common_speed` pseudo-register.
 *  @attention Pseudo-register task function
 *  @param speed Common motor speed.
 *  @return `ESP_OK` if successful.
 */
esp_err_t set_common_motor_speed(uint8_t speed) {
    _common_speed = speed;
    return ESP_OK;
}

/** @brief Update the motor directions `_motor_directions` pseudo-register.
 *  @attention Pseudo-register task function
 *  @param directions Array of motor directions.
 *  @return `ESP_OK` if successful.
 */
esp_err_t set_motor_directions(motor_direction_t* directions) {
    for (size_t i = 0; i < NUMBER_OF_MOTORS; i++) {
        _motor_directions[i] = directions[i];
    }

    return ESP_OK;
}
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

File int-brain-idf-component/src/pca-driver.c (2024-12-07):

#include "int-brain.h"

/** @file pca-driver.c
 *  @brief Implement the functions to interact with the PCA9635 driver, the I2C0-based PWM demux used to control the motor drivers and their corresponding LEDs.
 *  @brief https://www.nxp.com/docs/en/data-sheet/PCA9635.pdf
 *  @author @eccentricOrange
 */

/// @brief Fix the points below by reversing the PWM for the LED. Also remap the LED's PWM to leverage logarithmic perception
/// * for a high PWM: the motor is fast but the LED is dim
/// * for a low PWM: the motor is slow but the LED is bright
#define calculate_LED_PWM(PWM) (-(PCA_MAX_PWM_DUTY / PCA_MAX_LED_PWM) * (PWM - PCA_MAX_PWM_DUTY))

/** @brief Initialize the PCA9635 driver, by collecting many of the initialization functions defined in this file.
 *  @attention Direct task function
 *  @param bus_handle I2C bus handle.
 *  @return `ESP_OK` if successful.
 */
esp_err_t PCA_init(i2c_master_bus_handle_t bus_handle) {
    esp_err_t status = _PCA_add_driver_to_I2C0(bus_handle);
    if (status != ESP_OK) {
        return status;
    }

    status = _PCA_MOE_init();
    if (status != ESP_OK) {
        return status;
    }

    status = _PCA_enable_internal_drivers();
    if (status != ESP_OK) {
        return status;
    }

    status = _PCA_set_register(PCA_MODE1_ADDRESS, PCA_MODE1);
    if (status != ESP_OK) {
        return status;
    }

    return ESP_OK;
}

/** @brief Initialize the PCA9635 driver as an I2C device.
 *  @attention Direct task function
 *  @param bus_handle I2C bus handle.
 *  @return `ESP_OK` if successful.
 */
esp_err_t _PCA_add_driver_to_I2C0(i2c_master_bus_handle_t bus_handle) {
    const i2c_device_config_t PCA_I2C_config = {
        .dev_addr_length = I2C_ADDR_BIT_LEN_7,
        .device_address = PCA_DRIVER_ADDRESS,
        .scl_speed_hz = PCA_I2C0_SPEED};

    return i2c_master_bus_add_device(bus_handle, &PCA_I2C_config, &_PCA_I2C0_device_handle);
}

/** @brief Set the register of the PCA9635 driver.
 *  @attention Direct task function (in this case "register" a register on the PCA9635)
 *  @param register_address Register address to write to.
 *  @param data Data to write to the register.
 *  @return `ESP_OK` if successful.
 */
esp_err_t _PCA_set_register(uint8_t register_address, uint8_t data) {
    const uint8_t data_array[] = {register_address, data};
    return i2c_master_transmit(_PCA_I2C0_device_handle, &data_array, 2, PCA_I2C0_WRITE_TIMEOUT);
}

/** @brief Enable the LED drivers on the PCA9635 driver by setting their registers.
 *  @attention Direct task function
 *  @return `ESP_OK` if successful.
 */
esp_err_t _PCA_enable_internal_drivers() {
    for (uint8_t address_index = 0; address_index < PCA_NUMBER_OF_LED_DRIVERS; address_index++) {
        esp_err_t status = _PCA_set_register(PCA_LED_DRIVER_ADDRESS + address_index, PCA_ENABLE_DRIVERS);
        if (status != ESP_OK) {
            return status;
        }
    }
    return ESP_OK;
}

/** @brief Initialize the motor output enable (MOE) pin as an output. This enables/disables the PCA9635 driver.
 *  @attention Direct task function
 *  @return `ESP_OK` if successful.
 */
esp_err_t _PCA_MOE_init() {
    const gpio_config_t MOE_config = {
        .pin_bit_mask = 1 << PCA_MOTOR_ENABLE_PIN,
        .mode = GPIO_MODE_OUTPUT,
        .pull_up_en = GPIO_PULLUP_DISABLE,
        .pull_down_en = GPIO_PULLDOWN_DISABLE,
        .intr_type = GPIO_INTR_DISABLE,
    };

    return gpio_config(&MOE_config);
}

/** @brief Command an LED with a PWM value.
 *  @attention Direct task function
 *  @param motor Motor the LED indicates for.
 *  @param PWM PWM value for the LED.
 *  @return `ESP_OK` if successful.
 */
esp_err_t PCA_command_LED(motor_t motor, uint8_t PWM) {
    const uint8_t LED_data[] = {PWM0_REGISTER_ADDRESS + motor.LED_pin, calculate_LED_PWM(PWM)};
    return i2c_master_transmit(_PCA_I2C0_device_handle, &LED_data, 2, PCA_I2C0_WRITE_TIMEOUT);
}

/** @brief Command a motor with a PWM value, ignoring the LED. Motor PWMs are converted based on direction.
 *  @attention Direct task function
 *  @param motor Motor to command.
 *  @param direction Direction to move the motor.
 *  @param PWM PWM value for the motor.
 *  @return `ESP_OK` if successful.
 */
esp_err_t PCA_command_motor(motor_t motor, motor_direction_t direction, uint8_t PWM) {
    uint8_t PWM_1, PWM_2;
    esp_err_t status;

    direction_to_PWMs(direction, PWM, &PWM_1, &PWM_2);

    const uint8_t PWM1_data[] = {PWM0_REGISTER_ADDRESS + motor.output_pin_1, PWM_1};
    const uint8_t PWM2_data[] = {PWM0_REGISTER_ADDRESS + motor.output_pin_2, PWM_2};

    status = i2c_master_transmit(_PCA_I2C0_device_handle, &PWM1_data, 2, PCA_I2C0_WRITE_TIMEOUT);
    if (status != ESP_OK) {
        return status;
    }

    status = i2c_master_transmit(_PCA_I2C0_device_handle, &PWM2_data, 2, PCA_I2C0_WRITE_TIMEOUT);
    if (status != ESP_OK) {
        return status;
    }

    return ESP_OK;
}

/** @brief Command a motor and an LED with a PWM value. LED PWMs are re-scaled and motor PWMs are converted based on direction.
 *  @attention Direct task function
 *  @param motor Motor to command.
 *  @param direction Direction to move the motor.
 *  @param PWM PWM value for the motor.
 *  @return `ESP_OK` if successful.
 */
esp_err_t PCA_command_motor_with_LED(motor_t motor, motor_direction_t direction, uint8_t PWM) {
    uint8_t PWM_1, PWM_2;
    esp_err_t status;

    direction_to_PWMs(direction, PWM, &PWM_1, &PWM_2);

    const uint8_t PWM1_data[] = {PWM0_REGISTER_ADDRESS + motor.output_pin_1, PWM_1};
    const uint8_t PWM2_data[] = {PWM0_REGISTER_ADDRESS + motor.output_pin_2, PWM_2};
    const uint8_t LED_data[] = {PWM0_REGISTER_ADDRESS + motor.LED_pin, calculate_LED_PWM(PWM)};

    status = i2c_master_transmit(_PCA_I2C0_device_handle, &PWM1_data, 2, PCA_I2C0_WRITE_TIMEOUT);
    if (status != ESP_OK) {
        return status;
    }

    status = i2c_master_transmit(_PCA_I2C0_device_handle, &PWM2_data, 2, PCA_I2C0_WRITE_TIMEOUT);
    if (status != ESP_OK) {
        return status;
    }

    status = i2c_master_transmit(_PCA_I2C0_device_handle, &LED_data, 2, PCA_I2C0_WRITE_TIMEOUT);
    if (status != ESP_OK) {
        return status;
    }

    return ESP_OK;
}

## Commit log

2024-05-31 fin sch, fin placement
    [int-brain.kicad_pcb, int-brain.kicad_sch, motor-driver.kicad_sch]
2024-06-01 finish one iteration
    [int-brain.kicad_pcb, int-brain.kicad_sch]
2024-06-03 placed PCB components
    [int-brain.kicad_pcb, int-brain.kicad_sch, motor-driver.kicad_sch]
2024-06-03 made smaller
    [int-brain.kicad_pcb]
2024-06-03 routing attempt
    [int-brain.kicad_pcb, int-brain.kicad_sch]
2024-06-04 small routing improvements
    [int-brain.kicad_pcb]
2024-06-04 re-do pinouts based on code
    [int-brain.kicad_pcb, int-brain.kicad_sch]
2024-06-04 finish schematic rearrangement
    [int-brain.kicad_pcb, int-brain.kicad_sch]
2024-06-04 add formula
    [int-brain.kicad_pcb]
2024-06-05 set current sense resistors
    [int-brain.kicad_pcb, int-brain.kicad_sch, motor-driver.kicad_sch]
2024-06-08 done placement
    [int-brain.kicad_pcb, int-brain.kicad_sch, motor-driver.kicad_sch]
2024-06-08 done placement again
    [buck-converter.kicad_sch, int-brain.kicad_pcb, int-brain.kicad_sch]
2024-06-09 add cap to PCA ic
    [int-brain.kicad_pcb, int-brain.kicad_sch]
2024-06-09 some zone
    [int-brain.kicad_pcb]
2024-06-09 add solder point for PCA I/O
    [int-brain.kicad_pcb, int-brain.kicad_sch]
2024-06-16 minor improvements
    [buck-converter.kicad_sch, int-brain.kicad_pcb, int-brain.kicad_sch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]
2024-06-17 add pin-outs
2024-06-17 add LEDs
2024-06-17 link to README
    [int-brain.kicad_sch]
2024-06-17 footprint updates
    [buck-converter.kicad_sch, int-brain.kicad_pcb, int-brain.kicad_sch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]
2024-06-19 change I2C and minor updates
    [int-brain.kicad_pcb, int-brain.kicad_sch]
2024-07-02 basic redesign. PCB not up to date
    [int-brain.kicad_pcb, motor-driver-DRV8251A.kicad_sch]
2024-07-04 finally done?
    [int-brain.kicad_pcb, int-brain.kicad_sch, motor-driver-DRV8251A.kicad_sch]
2024-08-07 update for battery voltage?
2024-09-22 overhauled for UART
2024-09-22 overhaul for UART
2024-12-07 merged pcb repo
    [buck-converter.kicad_sch, int-brain.kicad_pcb, int-brain.kicad_sch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]
2024-12-07 clean up
    [buck-converter.kicad_sch, int-brain.kicad_pcb, int-brain.kicad_sch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]
